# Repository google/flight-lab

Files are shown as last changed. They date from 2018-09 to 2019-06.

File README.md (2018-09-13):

# Flight Lab

Flight Lab is a project to build high fidelity flight simulation experience.

Disclaimer: This is not an officially supported Google product.

# Flight Lab Repository

This repository contains complete spec, design, model, source code of software
and firmware to build a flight simulation system.

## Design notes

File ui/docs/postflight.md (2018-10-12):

| ENGINE SHUTDOWN | |
|--|--|
| 1. Throttle | IDLE |
| 2. AVIONICS Switch | (BUS 1 and BUS 2) OFF |
| 3. Mixture | IDLE CUTOFF, Wait until engine stops. |
| 4. IGNITION Switch | OFF |
| 5. MASTER Switch | (ALT and BAT) OFF |

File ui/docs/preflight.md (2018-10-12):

| preflight | |
|--|--|
| 1. IGNITION Switch | OFF |
| 2. AVIONICS Switch | (BUS 1 and BUS 2) OFF |
| 3. MASTER Switch | (ALT and BAT) OFF |
| 4. All Light Switches | OFF |
| 5. PITOT HEAT Switch | OFF |
| 6. Throttle | IDLE |
| 7. Mixture | IDLE CUTOFF |
| 8. FLAPS | UP |

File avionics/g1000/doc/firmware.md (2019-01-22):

# Flashing the firmware

1. Load firmware/g1000.ino into Arduino IDE.
2. Set your sketchbook location to the avionics directory (Under preferences).
3. Install support for the [Feather M0 Proto](https://learn.adafruit.com/adafruit-feather-m0-basic-proto/using-with-arduino-ide).
4. Comment out either "#define PFD" or "#define MFD" at the top of the file.
   If this will be the PFD, leave MFD commented.  Otherwise comment out PFD
   and uncomment MFD.
5. Connect the Arduino to your PC with a micro USB cable.
6. Set the board to "Feather M0 Proto" under "Tools > Board"
7. Set the port under "Tools > Port".
8. Select "Sketch > Upload".
9. Done!

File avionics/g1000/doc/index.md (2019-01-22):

# Building the G1000

* [Bill of Materials](bom.md)
* [Ordering the PCBs](pcb_order.md)
* [Fabrication and Assembly](fabrication.md)
* [Building the PCBs](pcb_build.md)
* [Flashing the firmware](firmware.md)

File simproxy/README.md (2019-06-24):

# Prerequisites

* Microsoft Flight Simulator X with SP2
* Microsoft Flight Simulator X SP2 SDK

If Prepar3D is used instead, please update SIMCONNECT_SDK_DIR in Makefile to "C:\Program Files (x86)\Lockheed Martin\Prepar3D [version]\Utilities\SimConnect SDK".

# Setup

From command line, run the following in simproxy directory:

```
    make init
```

## gRPC

SimProxy depends on gRPC and related libraries.

Currently building these dependencies on Windows platform is not automated yet. Files have to be manually copied to [github root]\build\grpc.

```
    TODO: automate building of grpc on Windows platform.
```

# Build 

From command line, run the following in simproxy directory:

```
    make build
```

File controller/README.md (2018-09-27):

# Controller

Controller is the backend of the simulation system. It coordinates all machines
and devices to perform tasks, such as turning on/off the sytem, collecting
status, etc.

There are two parts: server and client. All communication between server and
client is via [gRPC](https://github.com/grpc/grpc).

## Server

Server runs on a single machine and connects to all clients to act as central
control. It:

*   dispatches command to all clients
*   collect component status from all clients
*   serve http APIs to frontend/UI

## Client

Client runs on every machine and acts as worker for server. Based on
configuration, it:

*   loads components to control apps, devices, etc
*   reports status of components to server.

# Usage

## Prerequisites

### For Windows Platform

1.  Install Python 2.7

    Choose X86 version regardless if OS is 64bit.

2.  Install Make for Windows

    2.1. Download and install from
    http://gnuwin32.sourceforge.net/packages/make.htm

    2.2. Add "C:\Program Files (X86)\GnuWin32\bin" to System PATH

3.  Install Microsoft Visual C++ Compiler for Python 2.7

    https://www.microsoft.com/en-us/download/details.aspx?id=44266

## Build

1. Install all the dependencies:

	```shell
	make init
	```

1. Build source code:

	```shell
	make build
	```

## Install

To have server or client run automatically on reboot:

```shell
make install-client
```

```shell
make install-server
```

# Development

To run server or client manually:

```shell
make run-client
```

```shell
make run-server
```

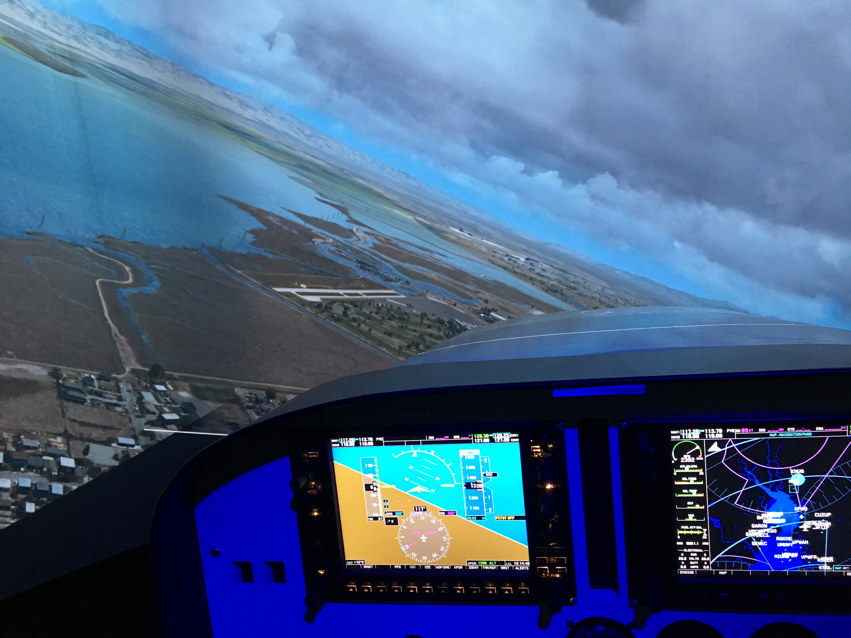
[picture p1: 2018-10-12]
ui/src/assets/bg.jpg

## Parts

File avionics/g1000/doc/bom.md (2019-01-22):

| Description | Quantity / G1000 | Manufacturer | Part Number | Link |
| --- | --- | --- | --- | --- |
| Arduino | 1 | Adafruit | Feather M0 Proto | [Adafruit](https://www.adafruit.com/products/2772)
| Button | 32 | C&K | KMT071 NGJ LHS | [Digikey](https://www.digikey.ca/product-detail/en/c-k/KMT071-NGJ-LHS/CKN10291CT-ND/2297282)
| Diode | 69 | Comchip Technology | CGRA4004-G | [Digikey](https://www.digikey.com/product-detail/en/comchip-technology/CGRA4004-G/641-1017-1-ND/1121139)
| 2 circuit OR gate | 1 | Fairchild Semi | NC7WZ32K8X | [Digikey](http://www.digikey.com/product-detail/en/fairchild-semiconductor/NC7WZ32K8X/NC7WZ32K8XCT-ND/965709)
| Rotary Encoder w/ Push | 3 | Bournes Inc | PEC11R-4215F-S0024 | [Digikey](https://www.digikey.com/product-detail/en/bourns-inc/PEC11R-4215F-S0024/PEC11R-4215F-S0024-ND/4499665)
| IDC Header | 4 | CNC Tech | 3020-20-0300-00 | [Digikey](https://www.digikey.com/product-detail/en/cnc-tech/3020-20-0300-00/1175-1623-ND/3441742)
| IDC Socket | 4 | CNC Tech | 3030-20-0103-00 | [Digikey](https://www.digikey.com/product-detail/en/cnc-tech/3030-20-0103-00/1175-1422-ND/3821475)
| Range Joystick | 1 | Grayhill | 60AD18-4-M-060C | [Digikey](https://www.digikey.com/products/en?mpart=60AD18-4-M-060C&v=136)
| Dual Rotary Encoder w/ Push | 5 | ELMA | E37-VT6330-1 | [Leobodnar](http://www.leobodnar.com/shop/index.php?main_page=product_info&cPath=98_75&products_id=196)
| Dual Knobs | 5 | ELMA | 020-4415 | [Leobodnar](http://www.leobodnar.com/shop/index.php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)
| LCD Controller | 1 | Chi Mei | M.NT68676.2A | [Ebay](http://www.ebay.com/itm/HDMI-VGA-DVI-lcd-Control-board-work-for-10-4inch-G104X1-L04-1024x768-lcd-panel-/181914630431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)
| LCD Panel | 1 | Chi Mei | G104XGE-L05 | [Ebay](https://www.ebay.com/sch/i.html?_from=R40&_trksid=m570.l1313&_nkw=G104XGE-L05&_sacat=0)
| LCD PSU | 1 | Chi Mei | | [Ebay](http://www.ebay.com/itm/New-12VDC-2-65A-40W-AC-Power-adapter-LCD-monitor-100VAC-240VAC-input-/181037711494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)

Note: The Grayhill 60A joystick can often be found on Ebay used for around $30.

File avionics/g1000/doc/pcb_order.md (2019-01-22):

# How To Order The Boards

## Chose a PCB Fabricator

Shop around with [PCBShopper](https://pcbshopper.com/) to find the best price
and quality.

## Upload the Gerber Files

Upload the following files one at a time to the PCB fabricator you've chosen:

* bottom/gerber_v3/bottom.zip
* left_side_autopilot/gerber_v3/left_side_auto.zip
* right_side/gerber_v3/right_side.zip

Note: Even if you don't want the GFC-700 autopilot, you should use the
left_side_autopilot files.  Just leave the autopilot buttons, diodes, and OR
gate unpopulated.  The files in left_side use a different kind of tactile
switch that proved very unreliable.

## Specify the PCB Parameters

* Layers: 2
* PCB thickness: 1.6mm
* Gold fingers: No
* Copper weight: 1oz

Note: This design contains internal cutouts.  Not all fabricators support
this.  We've had good results with both JLPCB and OSHPark.

You may want to order a solder stencil to save time.  We haven't done this,
but at times we wish we had.

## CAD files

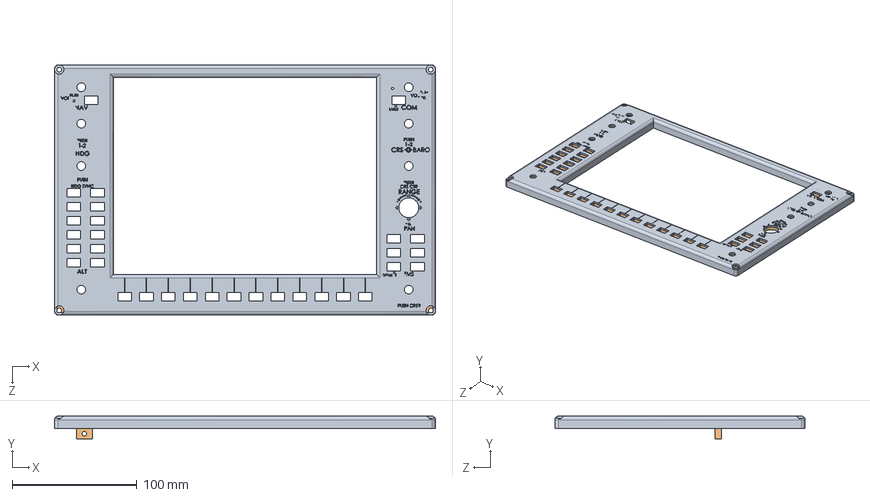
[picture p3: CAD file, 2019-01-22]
avionics/g1000/models/g1000_composite.SLDASM
306.0 x 18.4 x 201.0 mm
g1000
g1000_clear
g1000_text_new

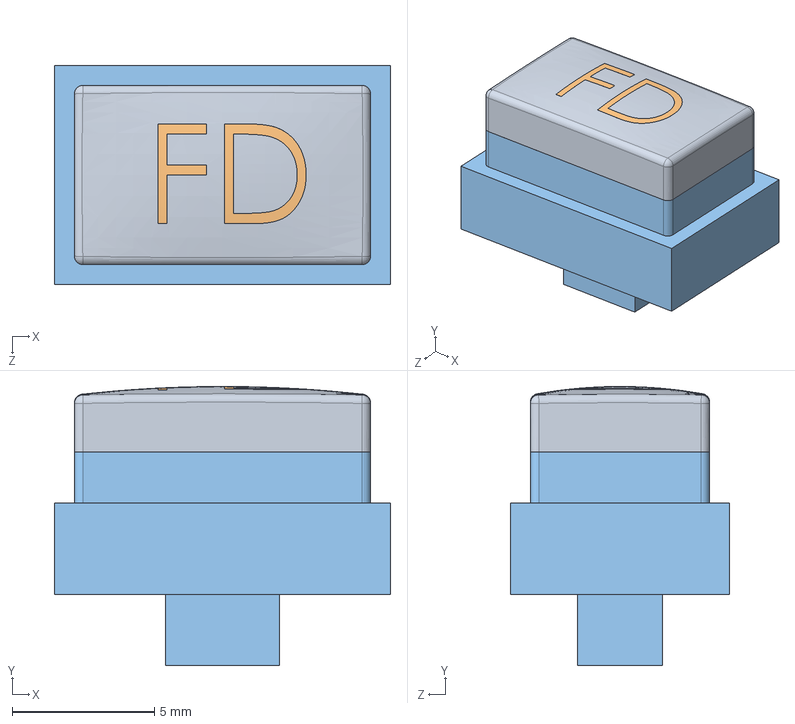
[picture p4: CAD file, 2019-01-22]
avionics/g1000/models/button_fd.SLDASM
11.8 x 9.80 x 7.70 mm
button_cap_fd
Part2^button_fd
button_base

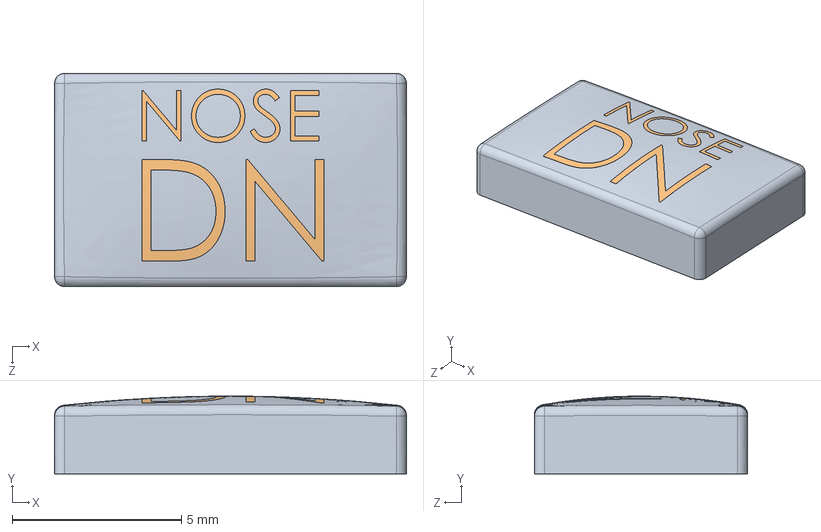
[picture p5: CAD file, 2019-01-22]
avionics/g1000/models/button_cap_down.SLDASM
10.4 x 2.30 x 6.30 mm
button_cap_down
Part11^button_cap_down

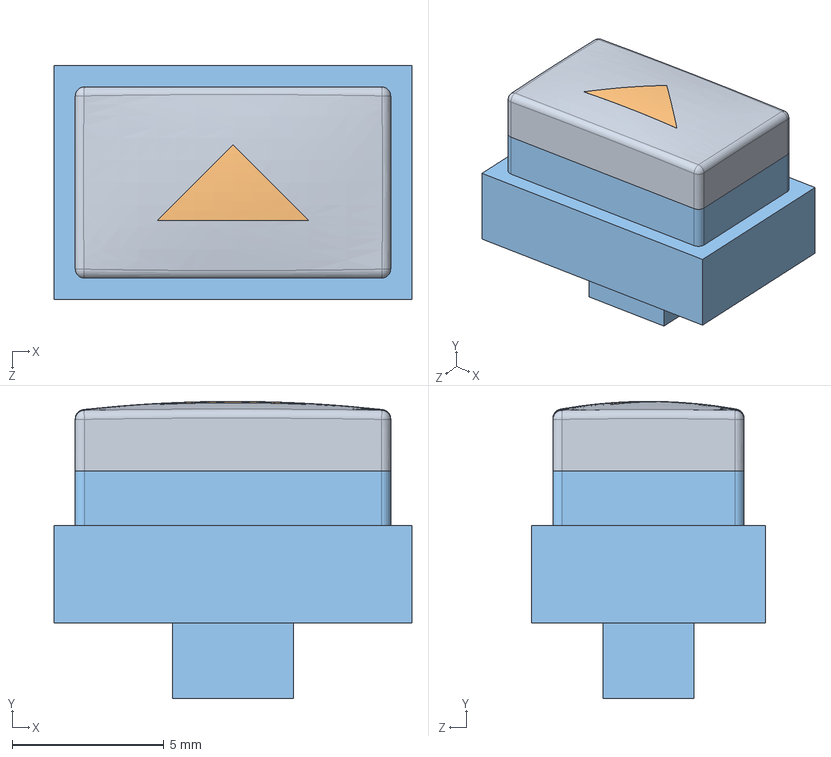
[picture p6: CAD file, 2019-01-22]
avionics/g1000/models/button_arrow.SLDASM
11.8 x 9.80 x 7.70 mm
button_cap_arrow
Part9^button_arrow
button_base

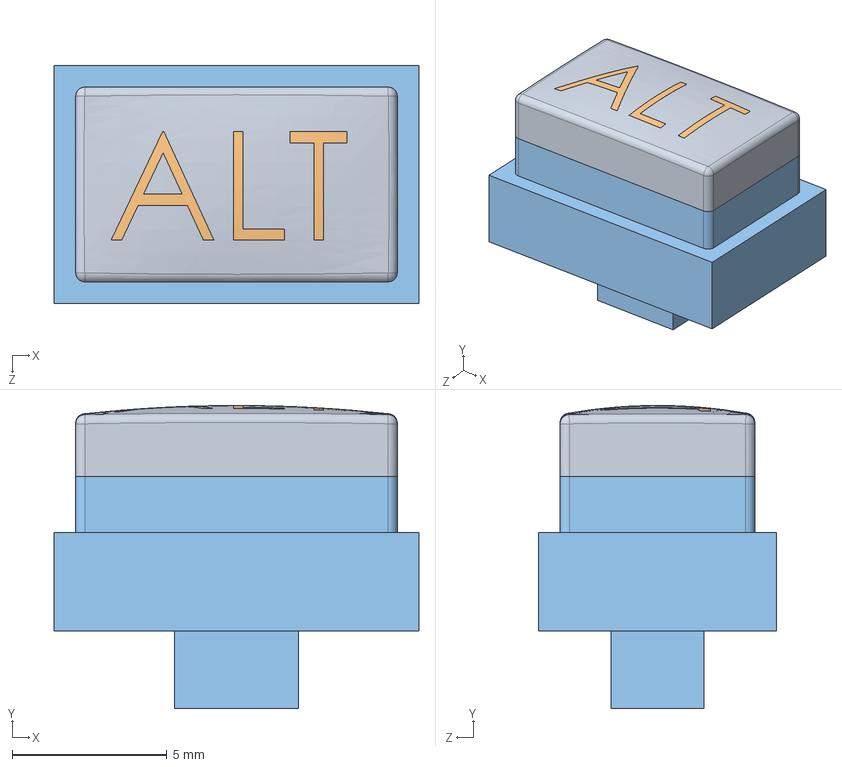
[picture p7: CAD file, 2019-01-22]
avionics/g1000/models/button_alt.SLDASM
11.8 x 9.80 x 7.70 mm
button_cap_alt
Part4^button_alt
button_base

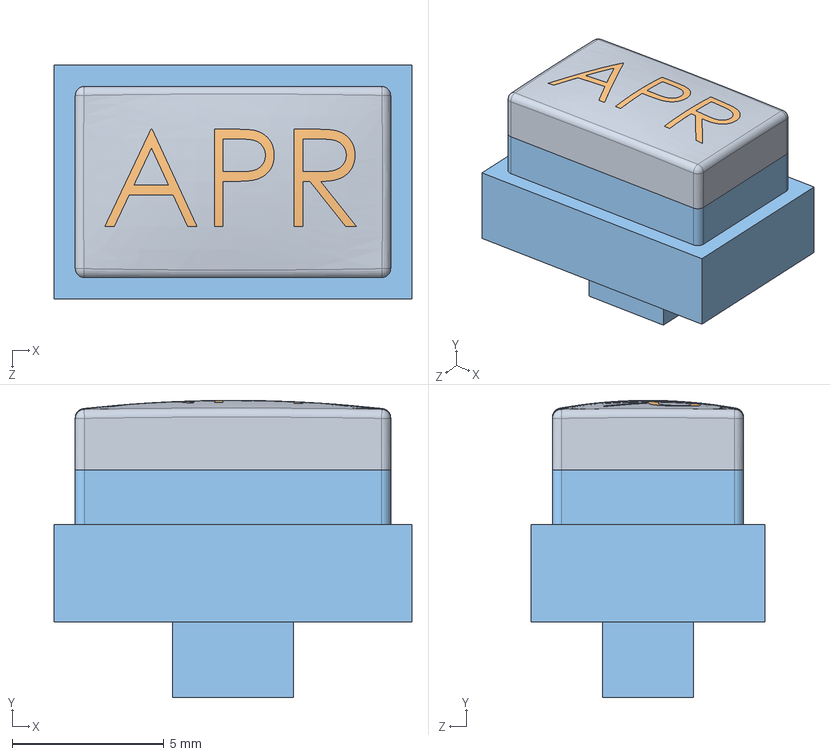
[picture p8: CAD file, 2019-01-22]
avionics/g1000/models/button_apr.SLDASM
11.8 x 9.80 x 7.70 mm
button_cap_apr
Part7^button_apr
button_base

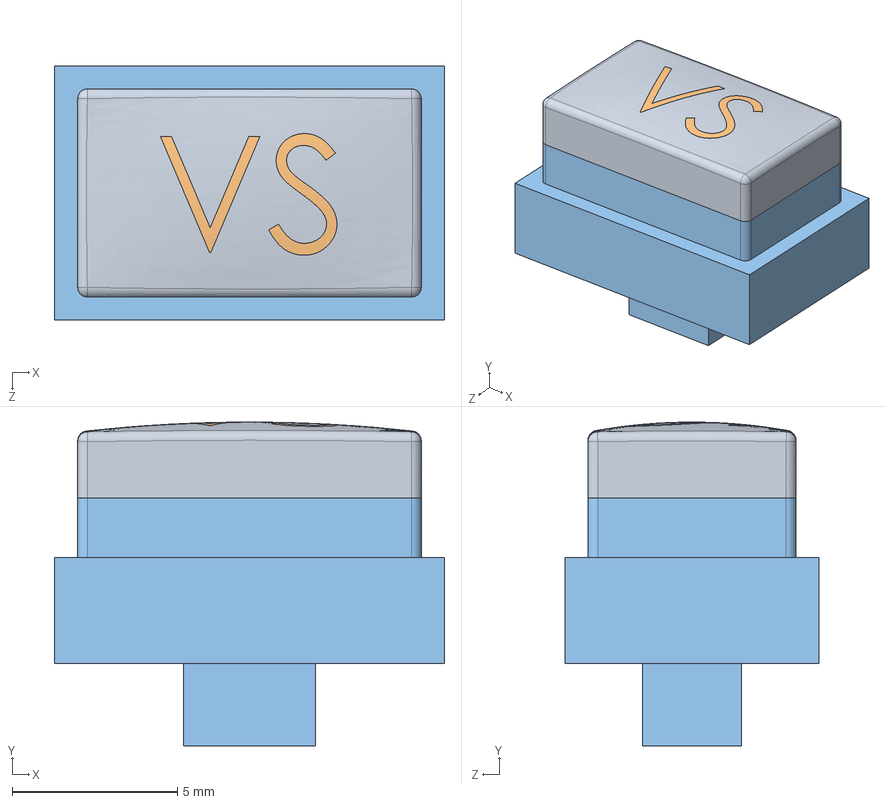
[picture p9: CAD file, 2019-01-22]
avionics/g1000/models/button_vs.SLDASM
11.8 x 9.80 x 7.70 mm
button_cap_vs
Part9^button_vs
button_base

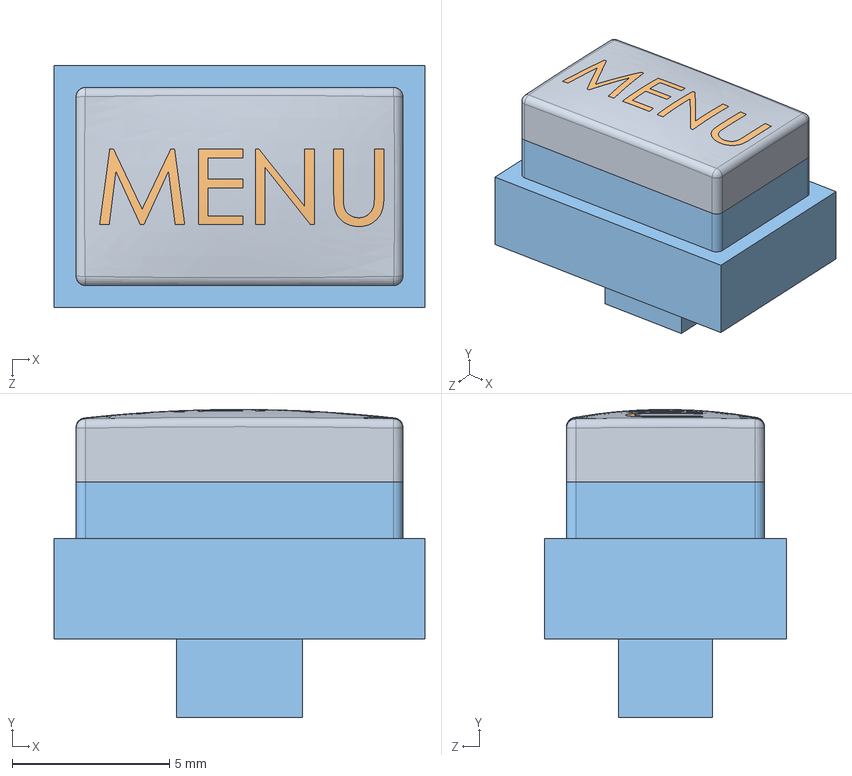
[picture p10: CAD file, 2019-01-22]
avionics/g1000/models/button_menu.SLDASM
11.8 x 9.80 x 7.70 mm
button_cap_menu
Part4^button_menu
button_base

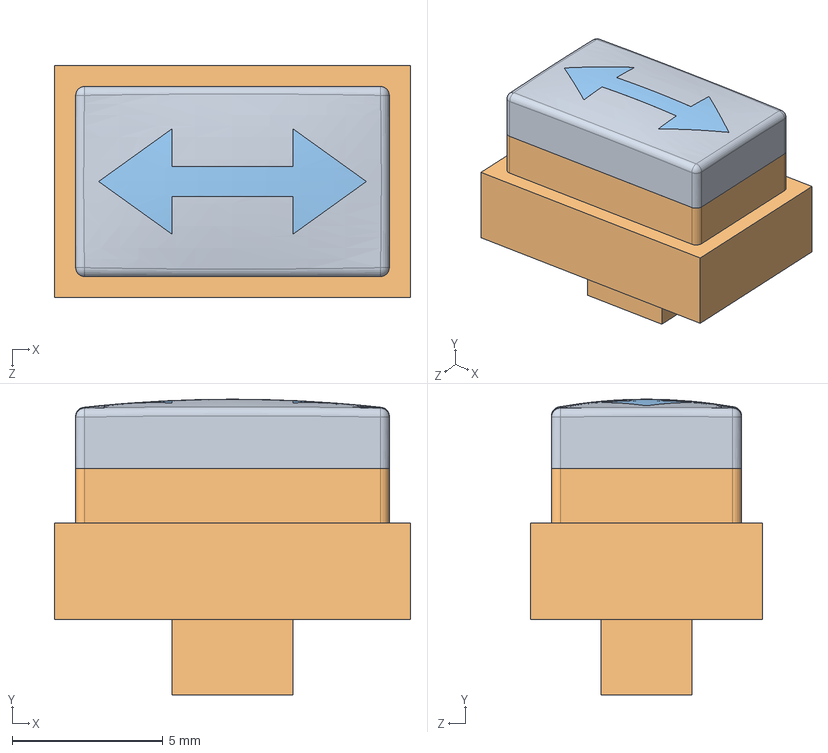
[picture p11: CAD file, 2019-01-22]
avionics/g1000/models/button_transfer.SLDASM
11.8 x 9.80 x 7.70 mm
button_cap_transfer
button_base
Part2^button_transfer

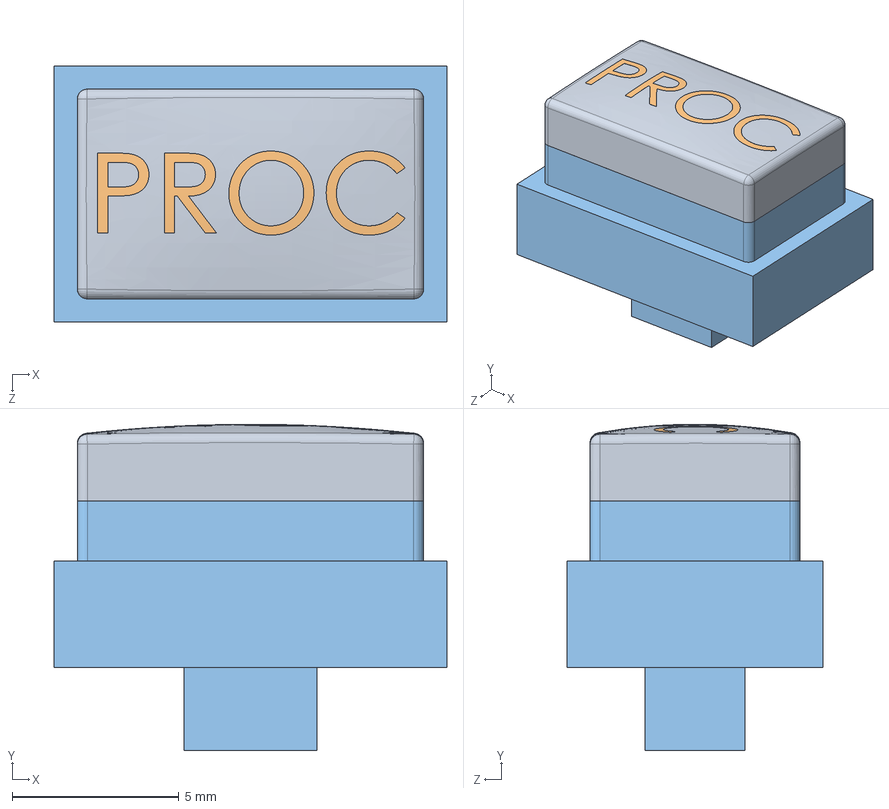
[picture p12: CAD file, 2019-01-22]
avionics/g1000/models/button_proc.SLDASM
11.8 x 9.80 x 7.70 mm
button_cap_proc
Part6^button_proc
button_base

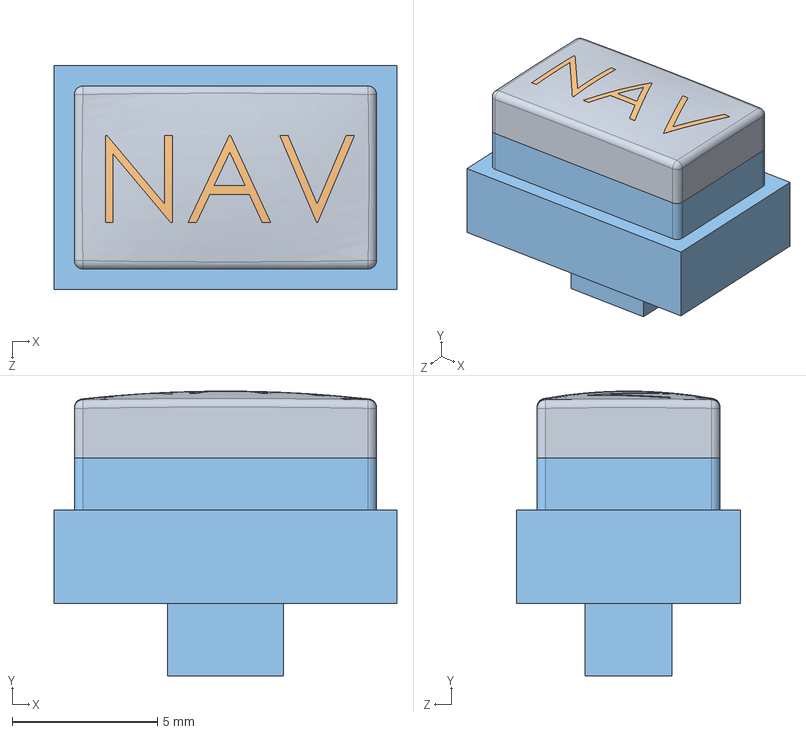
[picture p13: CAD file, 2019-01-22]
avionics/g1000/models/button_nav.SLDASM
11.8 x 9.80 x 7.70 mm
button_cap_nav
Part5^button_nav
button_base

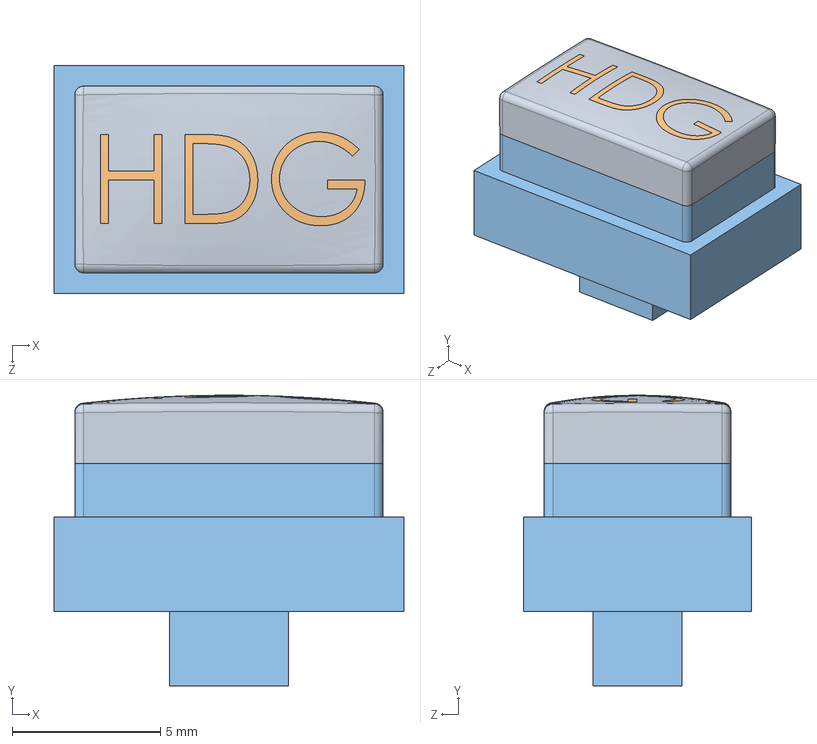
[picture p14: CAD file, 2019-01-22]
avionics/g1000/models/button_hdg.SLDASM
11.8 x 9.80 x 7.70 mm
button_cap_hdg
Part3^button_hdg
button_base

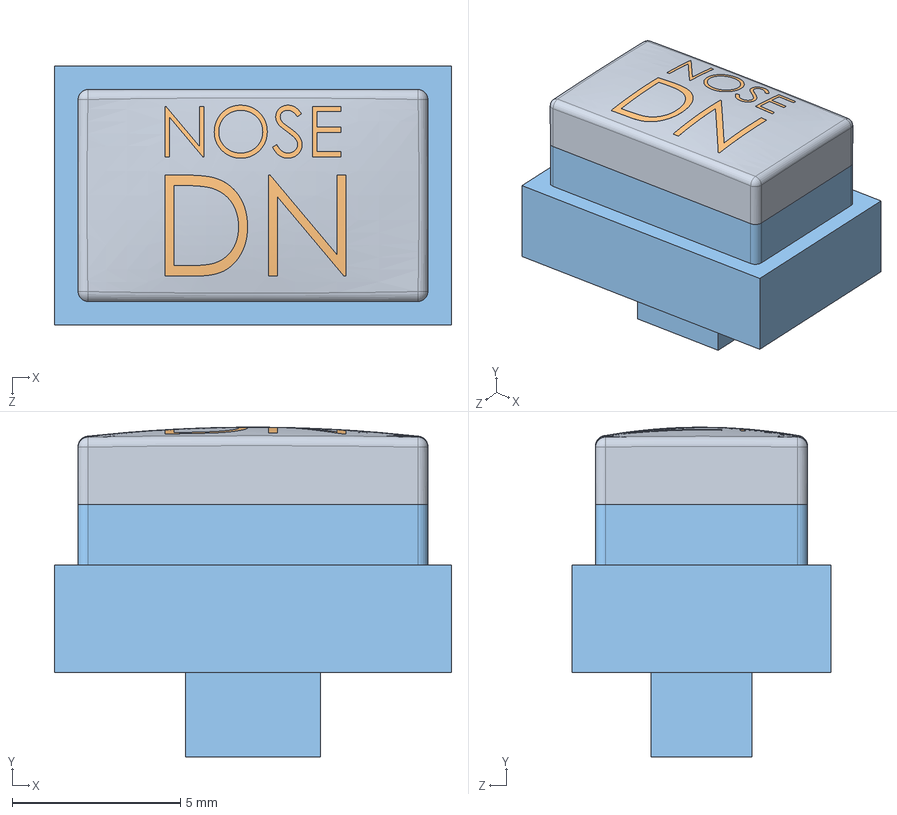
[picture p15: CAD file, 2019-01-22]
avionics/g1000/models/button_down.SLDASM
11.8 x 9.80 x 7.70 mm
button_cap_down
Part11^button_down
button_base

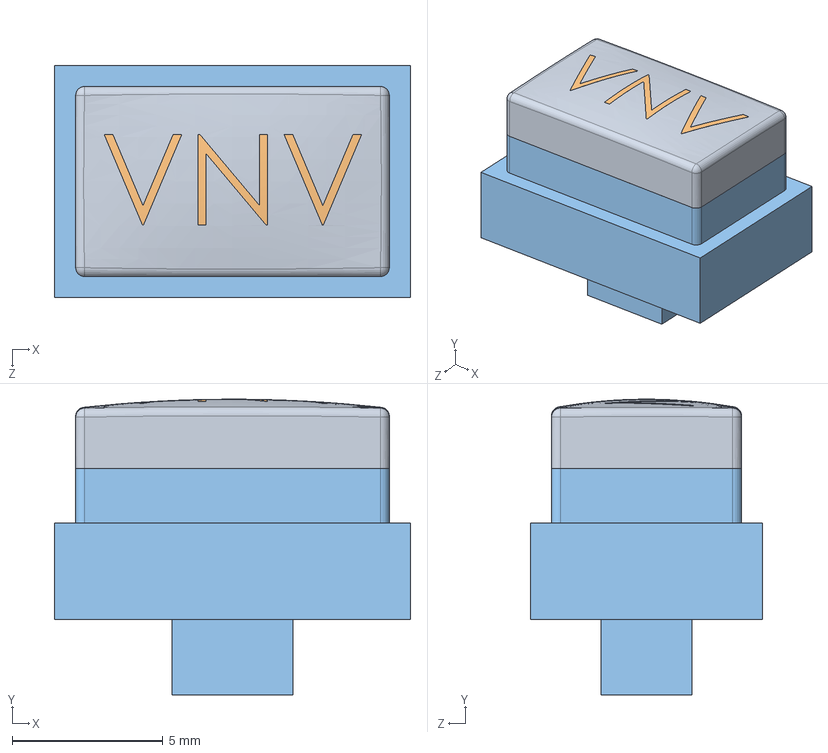
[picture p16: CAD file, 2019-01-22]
avionics/g1000/models/button_vnv.SLDASM
11.8 x 9.80 x 7.70 mm
button_cap_vnv
Part6^button_vnv
button_base

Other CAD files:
avionics/g1000/models/g1000_all.SLDASM
avionics/g1000/models/button_ap.SLDASM
avionics/g1000/models/button_clr.SLDASM
avionics/g1000/models/button_direct.SLDASM
avionics/g1000/models/button.SLDPRT
avionics/g1000/models/button_base.SLDPRT
avionics/g1000/models/button_bc.SLDASM
avionics/g1000/models/button_cap_alt.SLDPRT
avionics/g1000/models/button_cap_ap.SLDPRT
avionics/g1000/models/button_cap_apr.SLDPRT
avionics/g1000/models/button_cap_arrow.SLDPRT
avionics/g1000/models/button_cap_bc.SLDPRT
avionics/g1000/models/button_cap_clr.SLDPRT
avionics/g1000/models/button_cap_direct.SLDPRT
avionics/g1000/models/button_cap_down.SLDPRT
avionics/g1000/models/button_cap_ent.SLDPRT
avionics/g1000/models/button_cap_fd.SLDPRT
avionics/g1000/models/button_cap_flc.SLDPRT
avionics/g1000/models/button_cap_fpl.SLDPRT
avionics/g1000/models/button_cap_hdg.SLDPRT
avionics/g1000/models/button_cap_menu.SLDPRT
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

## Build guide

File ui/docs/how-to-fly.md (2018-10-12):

| engine start | |
|--|--|
| 1. Throttle | Open ¼ Inch |
| 2. MASTER Switch | (ALT and BAT) ON |
| 3. BEACON Light Switch | ON |
| 4. FUEL PUMP Switch | ON |
| 5. Mixture | FULL RICH |
| 6. FUEL PUMP Switch | OFF (after 3-5 seconds) |
| 7. IGNITION Switch | START Release when engine starts |
| 8. AVIONICS Switch | (BUS 1 and BUS 2) ON |

| before takeoff | |
|--|--|
| 1. Brake | APPLY |
| 2. Flight Controls | FREE and CORRECT |
| 3. Flight Instruments | CHECK (no red X’s) |
| 4. Altimeter | SET (PFD) |
| 5. ALT SEL | SET |
| 6. Standby Flight Instruments | CHECK |
| 7. Fuel Quantity | CHECK |
| 8. Mixture | RICH |
| 9. Elevator Trim | SET FOR TAKEOFF |
| 10. Throttle | 1800 RPM |
| 11. IGNITION Switch | CHECK L & R, drop < 150rpm, diff < 50rpm |
| 12. VAC Indicator | CHECK |
| 13. Engine Indicators | CHECK |
| 14. Ammeter & Voltmeter | CHECK |
| 15. Annunciators | CHECK |
| 16. Throttle | IDLE & CHECK |
| 17. Throttle | 1000 RPM |
| 18. COM Frequency | SET |
| 19. NAV Frequency | SET |
| 20. Flight Plan | As Desired |
| 21. Transponder | SET |
| 22. CDI Softkey | Select Nav Source |
| 22. FLAPS | UP to 10° |
| 23. STROBE Light Switch | ON |
| 24. Brake | RELEASE |

| NORMAL TAKEOFF | |
|--|--|
| 1. FLAPS | UP to 10° |
| 2. Throttle | FULL |
| 3. Mixture | RICH |
| 4. Elevator | Rotate at 55 KIAS |
| 5. Climb Airspeed | 70-80 KIAS |
| 6. FLAPS | RETRACT |

| ENROUTE CLIMB | |
|--|--|
| 1. Airspeed | 70 - 85 KIAS |
| 2. Throttle | FULL |
| 3. Mixture | RICH |

| CRUISE | |
|--|--|
| 1. Throttle | 2100 - 2700 RPM |
| 2. Elevator Trim | ADJUST |
| 3. Mixture | LEAN |

| DESCENT | |
|--|--|
| 1. Throttle | As Desired |
| 2. Mixture | ADJUST |
| 3. Altimeter | SET (PFD) |
| 4. ALT SEL | SET |
| 5. CDI Softkey | Select Nav Source |

| BEFORE LANDING | |
|--|--|
| 1. Mixture | RICH |
| 2. LAND & TAXI Light Switch | ON |

| NORMAL LANDING | |
|--|--|
| 1. Airspeed | 65 - 75 KIAS |
| 2. FLAPS | UP to 10° (<110 KIAS), 10° to FULL (<85 KIAS) |
| 3. Airspeed | 60 - 70 KIAS |
| 4. Elevator Trim | ADJUST |
| 5. Touchdown | Main Wheels First |
| 6. Landing Roll | Lower Nose Wheel Gently |
| 7. Brake | Minimum Required |

| AFTER LANDING | |
|--|--|
| 1. FLAPS | UP |
| 2. LAND Light Switch | OFF |
| 3. STROBE Light Switch | OFF |

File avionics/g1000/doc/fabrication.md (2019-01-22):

# Parts Fabrication

## Front Panel

There are a couple of options for fabricating the front panel.

### Using a multi-material 3d printer (preferrably SLA)

Pros:

* High quality result.
* Supports backlighting.
* Minimal post-processing.

Cons:

* Requires expensive equipment.

This approach requires a multi-material printer with very fine resolution.  The
printer will be creating small font text on the face plate, so precision is
essential.  These steps have been tested on an Objet500.

#### Print the parts

Print the following parts using the colors specified.  Look in models/v2_release
for the STL files.

* g1000_composite - g1000_clear-1.STL: 50/50 Clear and White

These two parts should be printed together.  Ensure that they share a common
origin.

* g1000_composite - g1000-1.STL: Black
* g1000_composite - g1000_ text_new-1.STL: White

The bulk of the frame is a 50/50 mix of clear and white.  This gives a good
compromise between light diffusion and transmission.

#### Finish the parts

* Use plastic scrapers and brushes under running water to remove the support
  material.
* Sand the front panel with 220 and then 400 grit sandpaper.
* Apply spray on clear coat.

#### Apply shielding

The one drawback of this approach is that the black frame is partially
translucent.  This means we need something to fully block the light in the
non-text areas.

We have had ok results using a layer of aluminum foil between the front panel
and the clear core.  The aluminum is cut to fit in the recess with an exacto
knife.  Then cutouts are added everywhere there is text or graphics.  This
blocks the light very well, but it is difficult to avoid tearing the foil.

In the future we may experiment with stencils and black spray paint or laser
cut paper shields.

### Using a desktop FDM 3D printer

Pros:

* Cheap
* May support backlighting

Cons:

* Labor intensive
* Experimental.

#### Print the parts

Print the following parts.  Look in models/v2_release for the STL files.

* left_side.STL
* right_side.STL

If you plan to use backlighting, these parts must be clear.  It is also
recommended that you use a high strength plastic with low warping such as
PETG.

#### Sanding and assembly

Sand until your hands ache.  It may also be worthwhile to use an expoxy filler
such as XTC-3D.  Then assemble the two halves using m3 square nuts and m3x25
hex socket cap screws.

#### Text options

* Print the text on a transparency sheet and glue the transparency to the frame.
  Then mask off the transparency and spray paint the rest of the frame black.
  Untested.
* Print the text on label paper and apply the labels to the frame.  Mask off the
  labels and spray paint the rest of the frame black.  Apply a layer of clear
  coat to seal the label to the frame.  This method is NOT compatible with
  backlighting.  Optional: Better results can be achieved by applying MANY
  layers of Mod Podge on top of the label before adding clear coat.  Eventually
  the label is encased in the Mod Podge and looks like it is part of the plastic
  frame.  Finish with clear coat.

## Buttons

### Using a multi-material 3d printer (preferrably SLA)

See the instructions for the face plate for more detail.  Each button should
be printed using the colors specified.  Look in models/v2_release
for the STL files.  Each button is made of three parts that must be printed
with a common origin.

* button_$NAME - button_base-1.STL: 50/50 clear and white
* button_$NAME - button_cap_$NAME-1.STL: Black
* button_$NAME - Part#^button_$NAME-1.STL: White

Here are the quantities needed:

* button_arrow: 12
* button_transfer: 2
* All other buttons: 1 each

### Using a desktop FDM 3D printer

In theory this could be done in the same manner as the frame.  However, doing
so would require an enormous amount of tedious labor.  This has not been
attempted.

## Monitor support

3D Print models/v2_release/screen_mount.STL.  Use whatever method is convenient.
If using an FDM printer, you'll need to generate supports in your slicer.

## Assembly

* Nest the clear frame core into the black face plate. Be sure to include
  the foil or paper light filter.
* If using backlighting, insert LED strip lighting into the channel around the
  edge with the LEDs facing inward.
* Insert all the buttons into their holes.
* Insert the three PCBs into their slots.  Attach with #6-32 screws.
* Attach the encoders to the frame with the nuts that came with them.
* Attach the monitor control boards to the monitor support with #6-32 and
  #4-40 screws.
* Lay the monitor on top of the back of the frame.  Lay the monitor support
  on top of it, aligning with the holes in the frame.
* Route the cables from the monitor control board to the monitor through the
  monitor support.
* Attach the monitor support to the frame with #6-32 screws.  Use caution around
  the ribbon cable on the right side.  It can bind against the monitor support
  and become damaged.
* The G1000 is complete!  Plug in the HDMI, power, and USB cables and test!
* Install into the instrument panel with #6-32 screws.

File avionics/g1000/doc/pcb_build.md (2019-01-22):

# Building the Boards

## Warning

If you haven't gotten the frame 3d printed yet, now is the time to do so.
You'll need it when you want to install the dual encoders.

## SMD Components

There are a large number of SMD components to install.  We highly recommend you
use solder paste and some combination of reflow and hot air instead of an iron.
It will save you a lot of time.

Pick a board, and start with the side that does not contain buttons. The buttons
are tiny and easily damaged by excess heat, so it's best to do them last.  We
use a pre-heater and hot air, so here's our process:

1. Lay down solder paste on all pads you intend to solder.  Don't worry if the
   paste isn't perfect or bridges.  It will fix itself when you apply heat.
2. Clamp the board on the pre-heater.
3. Lay the components down on the pads with fine tweezers.
4. Pre-heat the board to 180C.
5. Use a hot air gun at 250C to flow the solder.  Use the lowest air flow
   setting possible to avoid blowing the components around.
6. Turn off the pre-heater.

Repeat this process for the resistors and diodes on the other side.

**Pay careful attention to the polarity of the diodes.  A diode installed
backwards can be difficult to debug.  Make sure that the line on the diode is
installed on the same side as the line in the symbol on the PCB.**

## Teensy Tiny Buttons

Now you're ready to install the buttons.  These are essentially the same as
the other components, but greater care is warranted.  These buttons actually
specify that they should be installed according to this thermal profile:

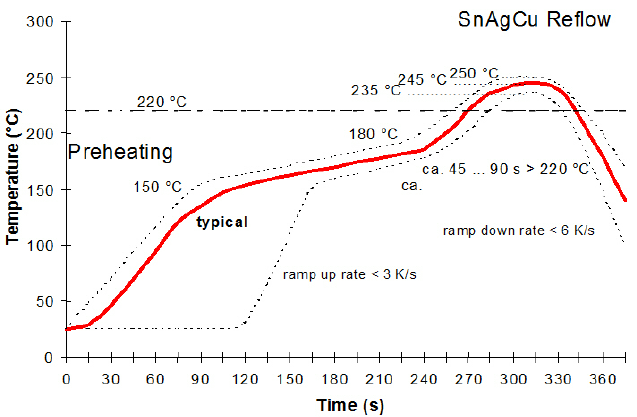
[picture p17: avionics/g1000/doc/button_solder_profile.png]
Button Thermal Profile


We used a timer and an infrared thermometer to match that profile as well as
our equipment was able.  Our experience was that the most critical part is to
keep the time spent above 200C as short as possible.  We were unable to ramp up
to 180C as fast as the chart specified, but that didn't seem to be a problem.
We didn't have to worry about ramp down speed since the board cooled slower than
6C/s even with all heat sources removed.

If you expose a button to excess heat, it will change color from pale yellow
to a brownish yellow.  This will cause the rubber dome to be brittle and it
will probably fail prematurely.  In this case, cover the other buttons with
Kapton tape and/or aluminum foil to shield them from more heat.  Then go
through the same heating steps as before to remove the bad component and
install a new one.  We found that the buttons could withstand several cycles
up to 180C without damage, but additional cycles to temperatures above 200C
caused problems.

## Pin Headers and Connectors

Install the pin headers and IDC connectors using a soldering iron.

## Caution

It's wise to do the encoder installs in stages because a mistake can cause
very odd errors that are hard to debug.  Start with a single encoder on the left
side.  Install the Arduino and make sure that encoder produces the expected
output on the serial port.  Then install another encoder and test.  After that,
connect the bottom board and test.  Finally connect the right board and install
those encoders one by one.

## Dual Encoders

The dual encoders stick through the holes in the PCB and are soldered to the
other side.  The thru-holes in the PCB are positioned so that they are offset
from the encoder pins by 2.54mm, which is the standard spacing for perfboard.

Buy some strip board and cut out 10 2x5 pieces.  The strips must run
along the short dimension so that you have 5 circuits with two holes each. The
easiest way to cut it is to clamp the boards in a vise with the lip of the
vise aligned with the cut you want to make.  Run a razor blade along the lip
of the vise 3 times on each side.  Then flex the board back and forth until it
breaks.

**Do not proceed further unless you have the 3d printed frame in hand!**

Place the dual encoders in the frame.  Refer to the pin labels on the back of
the encoders and the text on the PCB to make sure that the encoders are
installed right side up.  Once all the encoders are oriented correctly, place
the PCB in its slot in the frame.  Place a strip board on either side of an
encoder so that the encoder pins are connected to the pin headers on the PCB.
Securely fasten the encoder to the frame using the included nut.  Now you can
solder the pins to the perf board.  This procedure is necessary to make sure
the encoder sits at the correct height off of the PCB.

## Single Encoders

Solder the single encoders in place.  No special care is needed other than
making sure they sit flush on the PCB.

## Ribbon cables

TODO: Add notes here about the correct orientation.

## Joystick cable

TODO: Add notes about how to install the header on the joystick cable.

## Arduino Install

Solder the pin headers to the Arduino.  It's important to make sure they are
exactly vertical so it will fit in the socket on the board.  We recommend
putting the headers in a breadbord while soldering them to make sure they are
correct.

Install the Arduino on the left side PCB with the USB port facing down.

## Testing

Spin the encoders and push buttons while watching the serial console.  Make
sure you see all the events you expect and none that you don't.  If you
installed a diode backward, you may find that you will get spurious events
only when a certain encoder is in a certain position.  Thoroughly test each
encoder and its nearby components after you install each one.

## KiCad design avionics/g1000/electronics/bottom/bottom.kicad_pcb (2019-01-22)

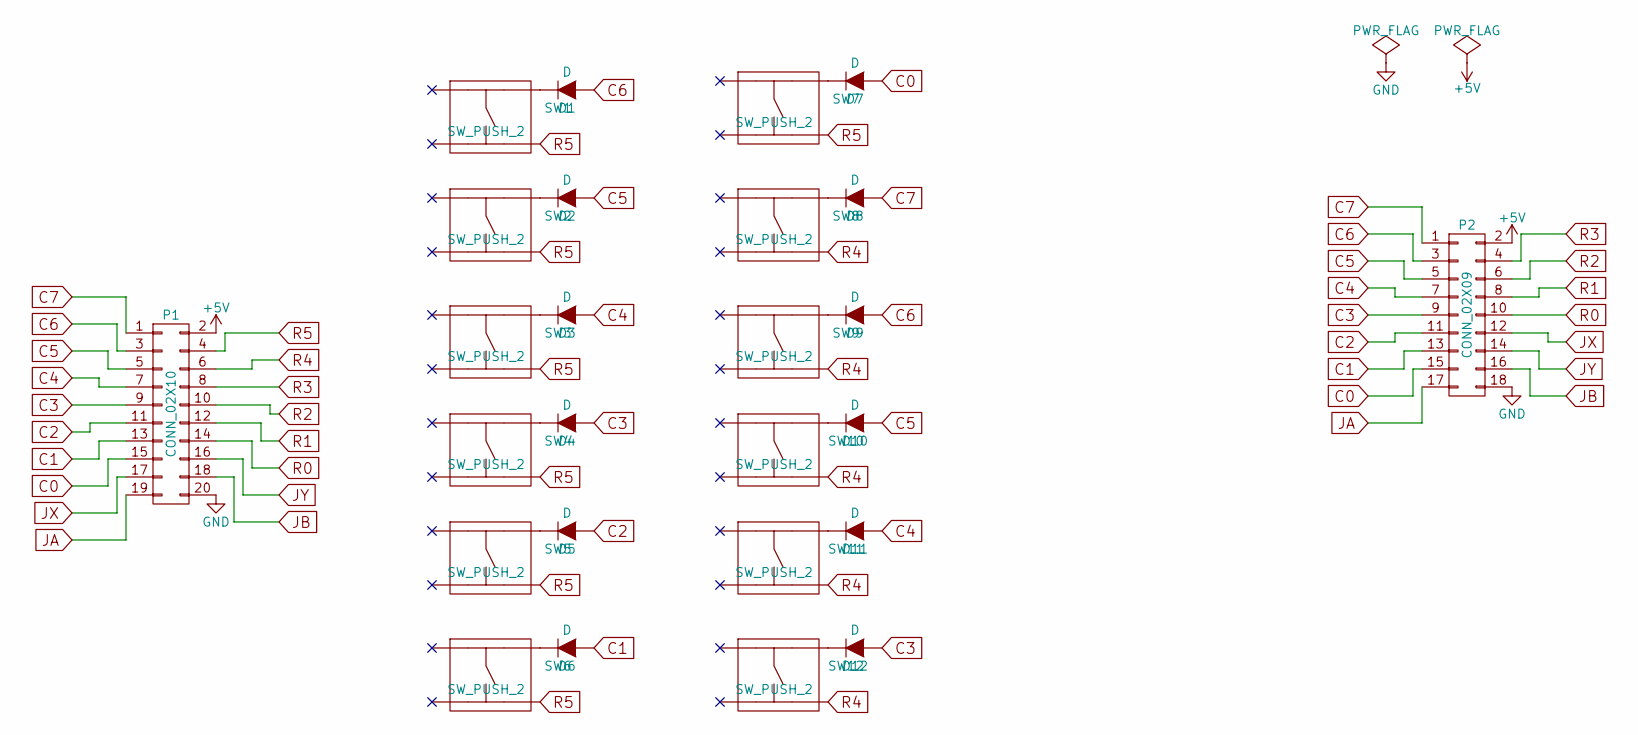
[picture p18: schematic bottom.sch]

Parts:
D1, D2, D3, D4, D5, D6, D7, D8, D9, D10, D11, D12: D; Diode_SMD
P1: CONN_02X10; CNC-3020-20
P2: CONN_02X09; CNC-3020-18
SW1, SW2, SW3, SW4, SW5, SW6, SW7, SW8, SW9, SW10, SW11, SW12: SW_PUSH_2; SW_PUSH

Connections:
+5V: P1.2, P2.2
C0: D7.2 (A), P1.15, P2.15
C1: D6.2 (A), P1.13, P2.13
C2: D5.2 (A), P1.11, P2.11
C3: D4.2 (A), D12.2 (A), P1.9, P2.9
C4: D3.2 (A), D11.2 (A), P1.7, P2.7
C5: D2.2 (A), D10.2 (A), P1.5, P2.5
C6: D1.2 (A), D9.2 (A), P1.3, P2.3
C7: D8.2 (A), P1.1, P2.1
GND: P1.20, P2.18
JA: P1.19, P2.17
JB: P1.18, P2.16
JX: P1.17, P2.12
JY: P1.16, P2.14
unnamed: D1.1 (K), SW1.2
unnamed: D2.1 (K), SW2.2
unnamed: D3.1 (K), SW3.2
unnamed: D4.1 (K), SW4.2
unnamed: D5.1 (K), SW5.2
unnamed: D6.1 (K), SW6.2
unnamed: D7.1 (K), SW7.2
unnamed: D8.1 (K), SW8.2
unnamed: D9.1 (K), SW9.2
unnamed: D10.1 (K), SW10.2
unnamed: D11.1 (K), SW11.2
unnamed: D12.1 (K), SW12.2
R0: P1.14, P2.10
R1: P1.12, P2.8
R2: P1.10, P2.6
R3: P1.8, P2.4
R4: P1.6, SW8.4, SW9.4, SW10.4, SW11.4, SW12.4
R5: P1.4, SW1.4, SW2.4, SW3.4, SW4.4, SW5.4, SW6.4, SW7.4

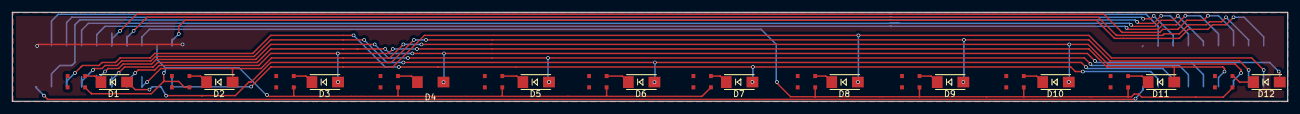
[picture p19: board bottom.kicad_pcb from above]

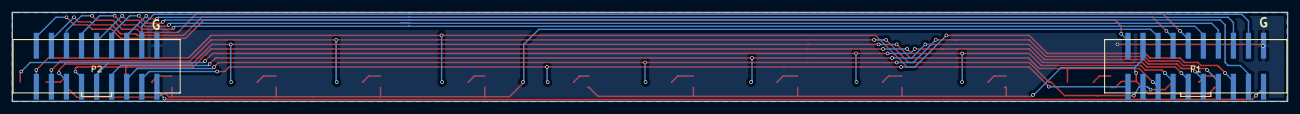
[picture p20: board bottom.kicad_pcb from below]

Board: 2 copper layers, 215.0 x 15.0 mm, 26 parts (2 on the bottom side), 32 nets.

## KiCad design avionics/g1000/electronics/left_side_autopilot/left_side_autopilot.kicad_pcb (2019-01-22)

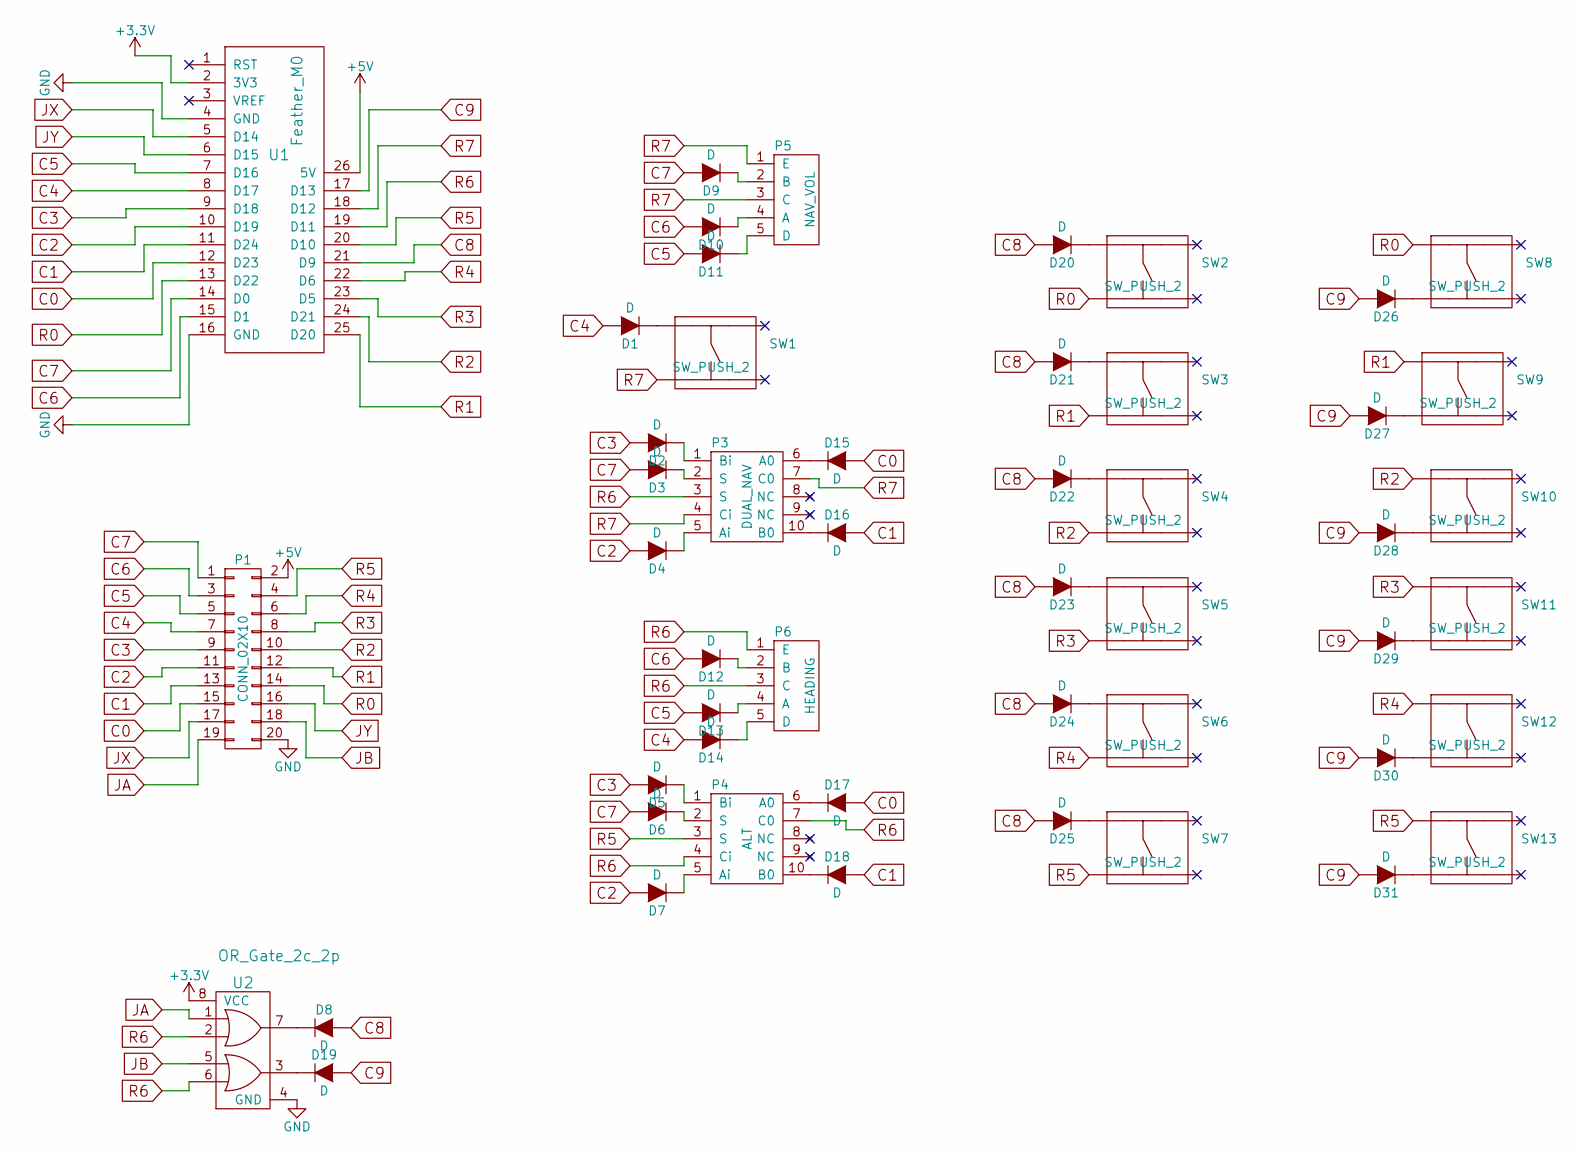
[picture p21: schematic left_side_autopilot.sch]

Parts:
D1, D2, D3, D4, D5, D6, D7, D8, D9, D10, D11, D12, D13, D14, D15, D16, D17, D18, D19, D20, D21, D22, D23, D24, D25, D26, D27, D28, D29, D30, D31: D; Diode_SMD
P1: CONN_02X10; CNC-3020-20
P3: DUAL_NAV; ELMA_conn
P4: ALT; ELMA_conn
P5: NAV_VOL; ENC_conn
P6: HEADING; ENC_conn
SW1, SW2, SW3, SW4, SW5, SW6, SW7, SW8, SW9, SW10, SW11, SW12, SW13: SW_PUSH_2; SW_PUSH
U1: Feather_M0; Feather_M0_SMD
U2: OR_Gate_2c_2p; NC7WZ32K8X

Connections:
+3V3: U1.2 (3V3), U2.8 (VCC)
+5V: P1.2, U1.26 (5V)
C0: D15.2 (A), D17.2 (A), P1.15, U1.12 (D23)
C1: D16.2 (A), D18.2 (A), P1.13, U1.11 (D24)
C2: D4.2 (A), D7.2 (A), P1.11, U1.10 (D19)
C3: D2.2 (A), D5.2 (A), P1.9, U1.9 (D18)
C4: D1.2 (A), D14.2 (A), P1.7, U1.8 (D17)
C5: D11.2 (A), D13.2 (A), P1.5, U1.7 (D16)
C6: D10.2 (A), D12.2 (A), P1.3, U1.15 (D1)
C7: D3.2 (A), D6.2 (A), D9.2 (A), P1.1, U1.14 (D0)
C8: D8.2 (A), D20.2 (A), D21.2 (A), D22.2 (A), D23.2 (A), D24.2 (A), D25.2 (A), U1.21 (D9)
C9: D19.2 (A), D26.2 (A), D27.2 (A), D28.2 (A), D29.2 (A), D30.2 (A), D31.2 (A), U1.17 (D13)
GND: P1.20, U1.4 (GND), U1.16 (GND), U2.4 (GND)
JA: P1.19, U2.1
JB: P1.18, U2.5
JX: P1.17, U1.5 (D14)
JY: P1.16, U1.6 (D15)
unnamed: D1.1 (K), SW1.1
unnamed: D2.1 (K), P3.1 (Bi)
unnamed: D3.1 (K), P3.2 (S)
unnamed: D4.1 (K), P3.5 (Ai)
unnamed: D5.1 (K), P4.1 (Bi)
unnamed: D6.1 (K), P4.2 (S)
unnamed: D7.1 (K), P4.5 (Ai)
unnamed: D8.1 (K), U2.7
unnamed: D9.1 (K), P5.2 (B)
unnamed: D10.1 (K), P5.4 (A)
unnamed: D11.1 (K), P5.5 (D)
unnamed: D12.1 (K), P6.2 (B)
unnamed: D13.1 (K), P6.4 (A)
unnamed: D14.1 (K), P6.5 (D)
unnamed: D15.1 (K), P3.6 (A0)
unnamed: D16.1 (K), P3.10 (B0)
unnamed: D17.1 (K), P4.6 (A0)
unnamed: D18.1 (K), P4.10 (B0)
unnamed: D19.1 (K), U2.3
unnamed: D20.1 (K), SW2.1
unnamed: D21.1 (K), SW3.1
unnamed: D22.1 (K), SW4.1
unnamed: D23.1 (K), SW5.1
unnamed: D24.1 (K), SW6.1
unnamed: D25.1 (K), SW7.1
unnamed: D26.1 (K), SW8.3
unnamed: D27.1 (K), SW9.3
unnamed: D28.1 (K), SW10.3
unnamed: D29.1 (K), SW11.3
unnamed: D30.1 (K), SW12.3
unnamed: D31.1 (K), SW13.3
R0: P1.14, SW2.3, SW8.1, U1.13 (D22)
R1: P1.12, SW3.3, SW9.1, U1.25 (D20)
R2: P1.10, SW4.3, SW10.1, U1.24 (D21)
R3: P1.8, SW5.3, SW11.1, U1.23 (D5)
R4: P1.6, SW6.3, SW12.1, U1.22 (D6)
R5: P1.4, P4.3 (S), SW7.3, SW13.1, U1.20 (D10)
R6: P3.3 (S), P4.4 (Ci), P4.7 (C0), P6.1 (E), P6.3 (C), U1.19 (D11), U2.2, U2.6
R7: P3.4 (Ci), P3.7 (C0), P5.1 (E), P5.3 (C), SW1.3, U1.18 (D12)

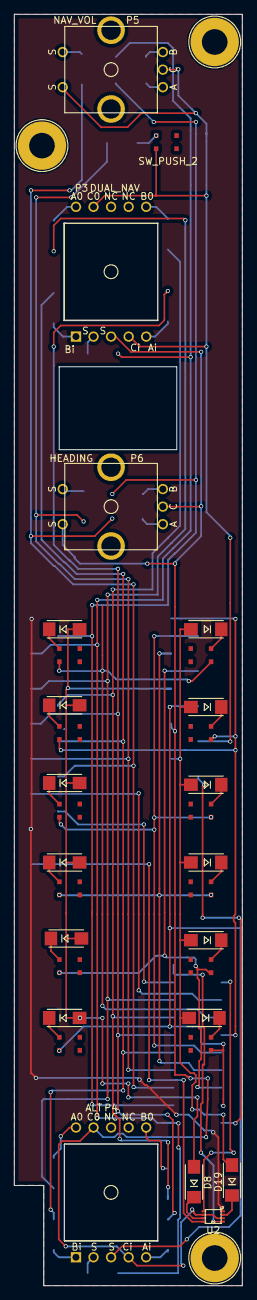
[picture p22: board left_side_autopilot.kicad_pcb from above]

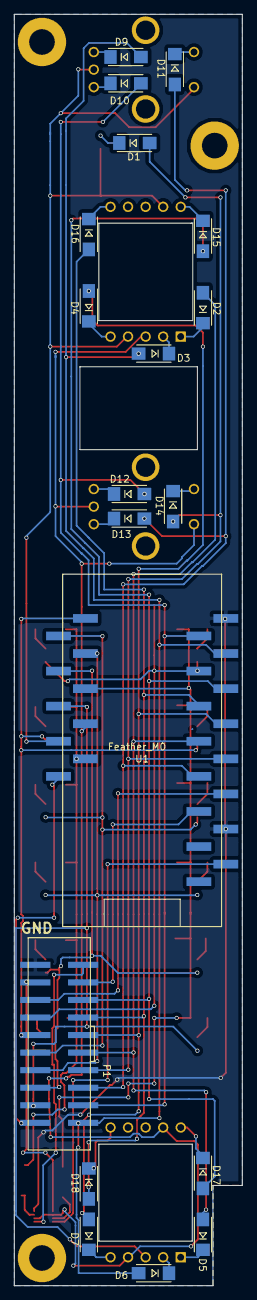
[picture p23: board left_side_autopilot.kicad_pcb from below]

Board: 2 copper layers, 33.0 x 184.0 mm, 54 parts (19 on the bottom side), 56 nets.

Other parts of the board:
Ref**: Val**; SCREW
Ref**#2, Ref**#3: Val**; SCREW

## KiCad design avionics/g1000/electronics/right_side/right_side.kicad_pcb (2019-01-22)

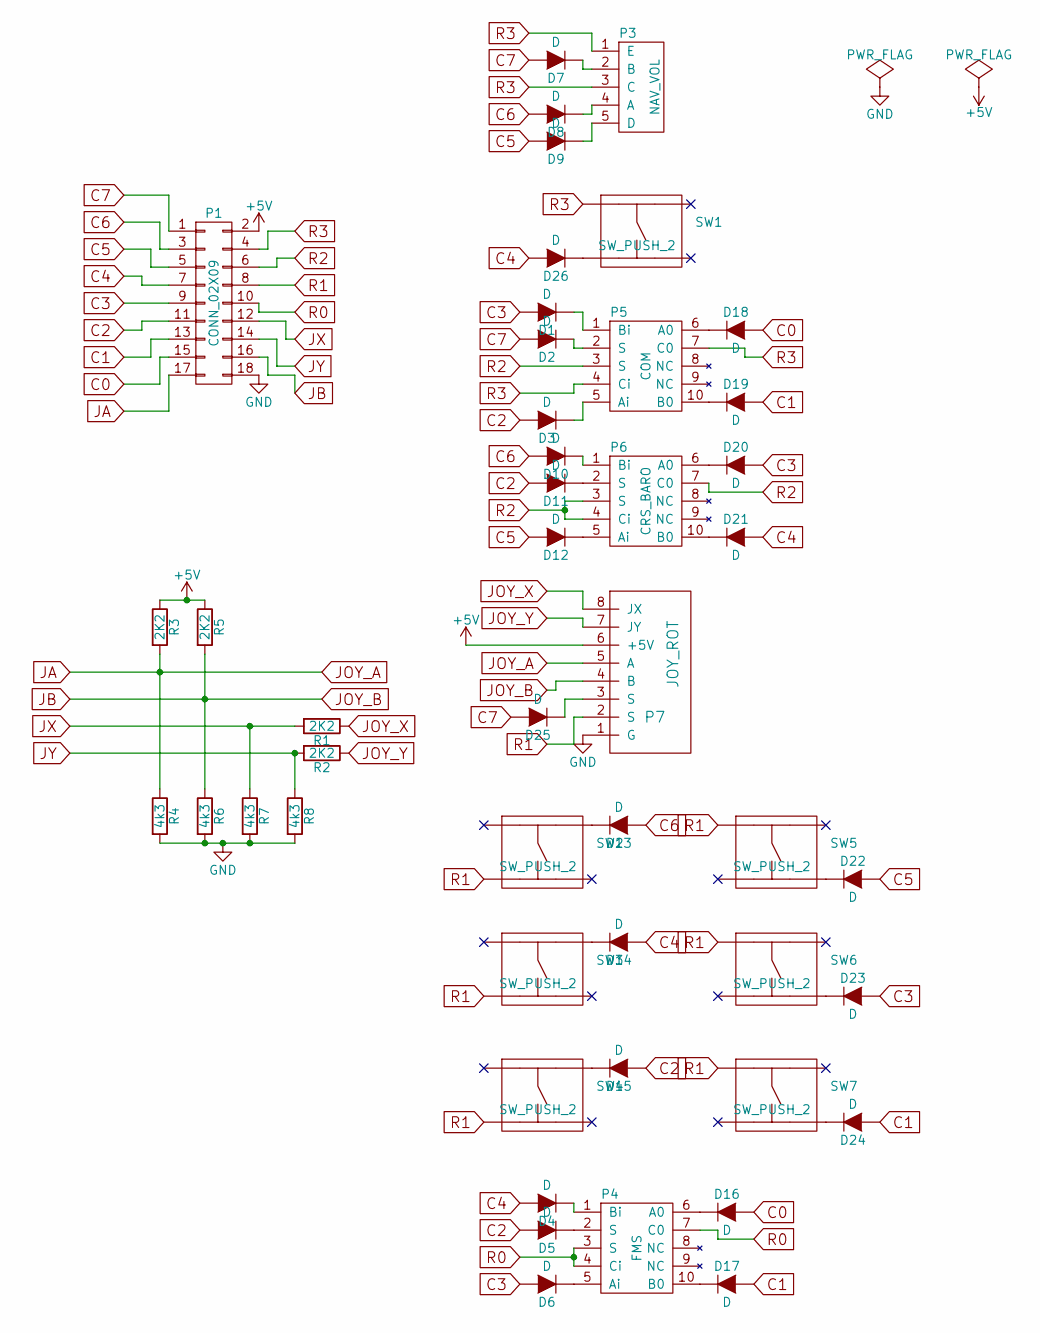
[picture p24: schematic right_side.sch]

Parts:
D1, D2, D3, D4, D5, D6, D7, D8, D9, D10, D11, D12, D13, D14, D15, D16, D17, D18, D19, D20, D21, D22, D23, D24, D25, D26: D; Diode_SMD
P1: CONN_02X09; CNC-3020-18
P3: NAV_VOL; ENC_conn
P4: FMS; ELMA_conn
P5: COM; ELMA_conn
P6: CRS_BARO; ELMA_conn
P7: JOY_ROT
R1, R2, R3, R5: 2K2; R_0805
R4, R6, R7, R8: 4k3; R_0805
SW1, SW2, SW3, SW4, SW5, SW6, SW7: SW_PUSH_2; SW_PUSH

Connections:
+5V: P1.2, P7.6 (+5V), R3.1, R5.1
C0: D16.2 (A), D18.2 (A), P1.15
C1: D17.2 (A), D19.2 (A), D24.2 (A), P1.13
C2: D3.2 (A), D5.2 (A), D11.2 (A), D15.2 (A), P1.11
C3: D1.2 (A), D6.2 (A), D20.2 (A), D23.2 (A), P1.9
C4: D4.2 (A), D14.2 (A), D21.2 (A), D26.2 (A), P1.7
C5: D9.2 (A), D12.2 (A), D22.2 (A), P1.5
C6: D8.2 (A), D10.2 (A), D13.2 (A), P1.3
C7: D2.2 (A), D7.2 (A), D25.2 (A), P1.1
GND: P1.18, P7.1 (G), R4.2, R6.2, R7.2, R8.2
JA: P1.17, P7.5 (A), R3.2, R4.1
JB: P1.16, P7.4 (B), R5.2, R6.1
JOY_X: P7.8 (JX), R1.1
JOY_Y: P7.7 (JY), R2.1
JX: P1.12, R1.2, R7.1
JY: P1.14, R2.2, R8.1
unnamed: D1.1 (K), P5.1 (Bi)
unnamed: D2.1 (K), P5.2 (S)
unnamed: D3.1 (K), P5.5 (Ai)
unnamed: D4.1 (K), P4.1 (Bi)
unnamed: D5.1 (K), P4.2 (S)
unnamed: D6.1 (K), P4.5 (Ai)
unnamed: D7.1 (K), P3.2 (B)
unnamed: D8.1 (K), P3.4 (A)
unnamed: D9.1 (K), P3.5 (D)
unnamed: D10.1 (K), P6.1 (Bi)
unnamed: D11.1 (K), P6.2 (S)
unnamed: D12.1 (K), P6.5 (Ai)
unnamed: D13.1 (K), SW2.2
unnamed: D14.1 (K), SW3.2
unnamed: D15.1 (K), SW4.2
unnamed: D16.1 (K), P4.6 (A0)
unnamed: D17.1 (K), P4.10 (B0)
unnamed: D18.1 (K), P5.6 (A0)
unnamed: D19.1 (K), P5.10 (B0)
unnamed: D20.1 (K), P6.6 (A0)
unnamed: D21.1 (K), P6.10 (B0)
unnamed: D22.1 (K), SW5.4
unnamed: D23.1 (K), SW6.4
unnamed: D24.1 (K), SW7.4
unnamed: D25.1 (K), P7.3 (S)
unnamed: D26.1 (K), SW1.3
R0: P1.10, P4.3 (S), P4.4 (Ci), P4.7 (C0)
R1: P1.8, P7.2 (S), SW2.3, SW3.3, SW4.3, SW5.1, SW6.1, SW7.1
R2: P1.6, P5.3 (S), P6.3 (S), P6.4 (Ci), P6.7 (C0)
R3: P1.4, P3.1 (E), P3.3 (C), P5.4 (Ci), P5.7 (C0), SW1.1

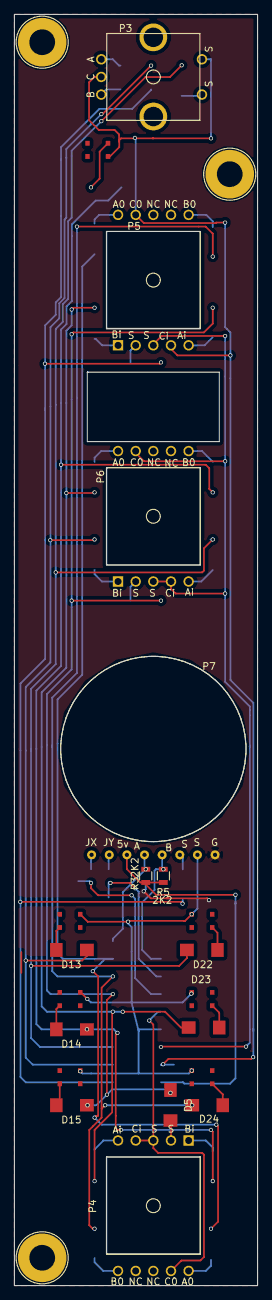
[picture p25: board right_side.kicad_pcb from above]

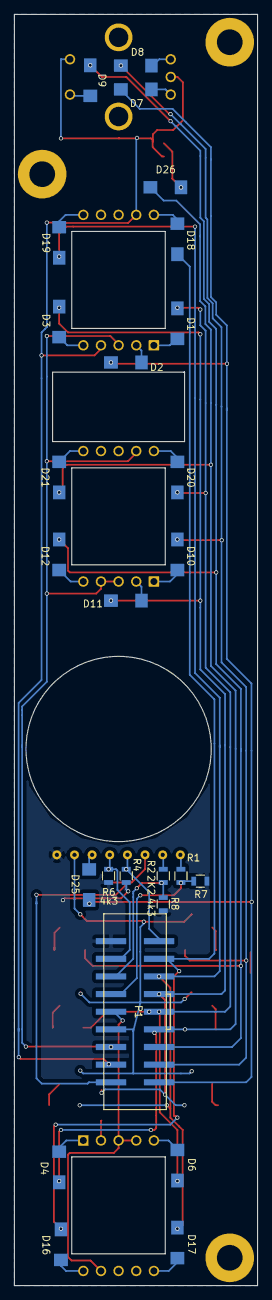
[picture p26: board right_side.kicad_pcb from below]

Board: 2 copper layers, 35.0 x 183.0 mm, 50 parts (26 on the bottom side), 46 nets.

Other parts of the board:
Ref**: Val**; SCREW
Ref**#2, Ref**#3: Val**; SCREW

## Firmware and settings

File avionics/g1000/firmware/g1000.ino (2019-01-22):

# Copyright 2018 Flight Lab authors.
#
# Licensed under the Apache License, Version 2.0 (the "License");
# you may not use this file except in compliance with the License.
# You may obtain a copy of the License at
#
#    https://www.apache.org/licenses/LICENSE-2.0
#
# Unless required by applicable law or agreed to in writing, software
# distributed under the License is distributed on an "AS IS" BASIS,
# WITHOUT WARRANTIES OR CONDITIONS OF ANY KIND, either express or implied.
# See the License for the specific language governing permissions and
# limitations under the License.

#include "../../shared/firmware/serial_rx/serial_rx.h"

#define PFD
// #define MFD

#define GFC700

#define MAX_OUT 16
#ifdef GFC700
#define MATRIX_COLS 10
#else
#define MATRIX_COLS 8
#endif
#define MATRIX_ROWS 8
#define MAX_COMMAND_LENGTH 32
#define KEY_ENTER 176

// Mapping from physical pins to matrix column and row indices.
#ifdef GFC700
//                                 0   1   2   3   4   5   6   7  8  9
const PROGMEM int kRowPins[] =    {22, 20, 21, 5,  6,  10, 11, 12};
const PROGMEM int kColumnPins[] = {23, 24, 19, 18, 17, 16, 1,  0, 9, 13};
#else
//                                 0   1   2   3   4   5   6   7
const PROGMEM int kRowPins[] =    {22, 20, 21, 5,  6,  10, 11, 12};
const PROGMEM int kColumnPins[] = {23, 24, 19, 18, 17, 16, 1,  0};
#endif

#ifdef PFD
#define IDENTIFIER "PFD"
#endif
#ifdef MFD
#define IDENTIFIER "MFD"
#endif

const PROGMEM char NAV_ID_TOGGLE[] = "NAV_ID_TOGGLE";
const PROGMEM char HDG_INCR[] = "HDG_INCR";
const PROGMEM char HDG_DECR[] = "HDG_DECR";
const PROGMEM char HDG_PRESS[] = "HDG_PRESS";
const PROGMEM char LARGE_ALT_INCR[] = "LARGE_ALT_INCR";
const PROGMEM char LARGE_ALT_DECR[] = "LARGE_ALT_DECR";
const PROGMEM char SMALL_ALT_INCR[] = "SMALL_ALT_INCR";
const PROGMEM char SMALL_ALT_DECR[] = "SMALL_ALT_DECR";
const PROGMEM char SMALL_ALT_PRESS[] = "SMALL_ALT_PRESS";
const PROGMEM char CRS_INCR[] = "CRS_INCR";
const PROGMEM char CRS_DECR[] = "CRS_DECR";
const PROGMEM char CRS_PRESS[] = "CRS_PRESS";
#ifdef PFD
const PROGMEM char NAV_FREQ_TOGGLE[] = "NAV_FREQ_TOGGLE";
const PROGMEM char LARGE_NAV_INCR[] = "LARGE_NAV_INCR";
const PROGMEM char LARGE_NAV_DECR[] = "LARGE_NAV_DECR";
const PROGMEM char SMALL_NAV_INCR[] = "SMALL_NAV_INCR";
const PROGMEM char SMALL_NAV_DECR[] = "SMALL_NAV_DECR";
const PROGMEM char SMALL_NAV_PRESS[] = "SMALL_NAV_PRESS";
const PROGMEM char COM_FREQ_TOGGLE[] = "COM_FREQ_TOGGLE";
const PROGMEM char COM_FREQ_TOGGLE_HOLD[] = "COM_FREQ_TOGGLE_HOLD";
const PROGMEM char LARGE_COM_INCR[] = "LARGE_COM_INCR";
const PROGMEM char LARGE_COM_DECR[] = "LARGE_COM_DECR";
const PROGMEM char SMALL_COM_INCR[] = "SMALL_COM_INCR";
const PROGMEM char SMALL_COM_DECR[] = "SMALL_COM_DECR";
const PROGMEM char SMALL_COM_PRESS[] = "SMALL_COM_PRESS";
const PROGMEM char BARO_INCR[] = "BARO_INCR";
const PROGMEM char BARO_DECR[] = "BARO_DECR";
const PROGMEM char RANGE_INCR[] = "PFD_RANGE_INCR";
const PROGMEM char RANGE_DECR[] = "PFD_RANGE_DECR";
const PROGMEM char RANGE_PRESS[] = "PFD_RANGE_PRESS";
const PROGMEM char RANGE_PAN_UP[] = "PFD_RANGE_PAN_UP";
const PROGMEM char RANGE_PAN_DOWN[] = "PFD_RANGE_PAN_DOWN";
const PROGMEM char RANGE_PAN_LEFT[] = "PFD_RANGE_PAN_LEFT";
const PROGMEM char RANGE_PAN_RIGHT[] = "PFD_RANGE_PAN_RIGHT";
const PROGMEM char DIRECT_TO[] = "PFD_DIRECT_TO";
const PROGMEM char MENU[] = "PFD_MENU";
const PROGMEM char FPL[] = "PFD_FPL";
const PROGMEM char PROC[] = "PFD_PROC";
const PROGMEM char CLR[] = "PFD_CLR";
const PROGMEM char ENT[] = "PFD_ENT";
const PROGMEM char LARGE_FMS_INCR[] = "PFD_LARGE_FMS_INCR";
const PROGMEM char LARGE_FMS_DECR[] = "PFD_LARGE_FMS_DECR";
const PROGMEM char SMALL_FMS_INCR[] = "PFD_SMALL_FMS_INCR";
const PROGMEM char SMALL_FMS_DECR[] = "PFD_SMALL_FMS_DECR";
const PROGMEM char SMALL_FMS_PRESS[] = "PFD_SMALL_FMS_PRESS";
const PROGMEM char SOFTKEY_1[] = "PFD_SOFTKEY_1";
const PROGMEM char SOFTKEY_2[] = "PFD_SOFTKEY_2";
const PROGMEM char SOFTKEY_3[] = "PFD_SOFTKEY_3";
const PROGMEM char SOFTKEY_4[] = "PFD_SOFTKEY_4";
const PROGMEM char SOFTKEY_5[] = "PFD_SOFTKEY_5";
const PROGMEM char SOFTKEY_6[] = "PFD_SOFTKEY_6";
const PROGMEM char SOFTKEY_7[] = "PFD_SOFTKEY_7";
const PROGMEM char SOFTKEY_8[] = "PFD_SOFTKEY_8";
const PROGMEM char SOFTKEY_9[] = "PFD_SOFTKEY_9";
const PROGMEM char SOFTKEY_10[] = "PFD_SOFTKEY_10";
const PROGMEM char SOFTKEY_11[] = "PFD_SOFTKEY_11";
const PROGMEM char SOFTKEY_12[] = "PFD_SOFTKEY_12";
#endif  // PFD
#ifdef MFD
const PROGMEM char NAV_FREQ_TOGGLE[] = "MFD_NAV_FREQ_TOGGLE";
const PROGMEM char LARGE_NAV_INCR[] = "MFD_LARGE_NAV_INCR";
const PROGMEM char LARGE_NAV_DECR[] = "MFD_LARGE_NAV_DECR";
const PROGMEM char SMALL_NAV_INCR[] = "MFD_SMALL_NAV_INCR";
const PROGMEM char SMALL_NAV_DECR[] = "MFD_SMALL_NAV_DECR";
const PROGMEM char SMALL_NAV_PRESS[] = "MFD_SMALL_NAV_PRESS";
const PROGMEM char COM_FREQ_TOGGLE[] = "MFD_COM_FREQ_TOGGLE";
const PROGMEM char COM_FREQ_TOGGLE_HOLD[] = "MFD_COM_FREQ_TOGGLE_HOLD";
const PROGMEM char LARGE_COM_INCR[] = "MFD_LARGE_COM_INCR";
const PROGMEM char LARGE_COM_DECR[] = "MFD_LARGE_COM_DECR";
const PROGMEM char SMALL_COM_INCR[] = "MFD_SMALL_COM_INCR";
const PROGMEM char SMALL_COM_DECR[] = "MFD_SMALL_COM_DECR";
const PROGMEM char SMALL_COM_PRESS[] = "MFD_SMALL_COM_PRESS";
const PROGMEM char BARO_INCR[] = "MFD_BARO_INCR";
const PROGMEM char BARO_DECR[] = "MFD_BARO_DECR";
const PROGMEM char RANGE_INCR[] = "MFD_RANGE_INCR";
const PROGMEM char RANGE_DECR[] = "MFD_RANGE_DECR";
const PROGMEM char RANGE_PRESS[] = "MFD_RANGE_PRESS";
const PROGMEM char RANGE_PAN_UP[] = "MFD_RANGE_PAN_UP";
const PROGMEM char RANGE_PAN_DOWN[] = "MFD_RANGE_PAN_DOWN";
const PROGMEM char RANGE_PAN_LEFT[] = "MFD_RANGE_PAN_LEFT";
const PROGMEM char RANGE_PAN_RIGHT[] = "MFD_RANGE_PAN_RIGHT";
const PROGMEM char DIRECT_TO[] = "MFD_DIRECT_TO";
const PROGMEM char MENU[] = "MFD_MENU";
const PROGMEM char FPL[] = "MFD_FPL";
const PROGMEM char PROC[] = "MFD_PROC";
const PROGMEM char CLR[] = "MFD_CLR";
const PROGMEM char ENT[] = "MFD_ENT";
const PROGMEM char LARGE_FMS_INCR[] = "MFD_LARGE_FMS_INCR";
const PROGMEM char LARGE_FMS_DECR[] = "MFD_LARGE_FMS_DECR";
const PROGMEM char SMALL_FMS_INCR[] = "MFD_SMALL_FMS_INCR";
const PROGMEM char SMALL_FMS_DECR[] = "MFD_SMALL_FMS_DECR";
const PROGMEM char SMALL_FMS_PRESS[] = "MFD_SMALL_FMS_PRESS";
const PROGMEM char SOFTKEY_1[] = "MFD_SOFTKEY_1";
const PROGMEM char SOFTKEY_2[] = "MFD_SOFTKEY_2";
const PROGMEM char SOFTKEY_3[] = "MFD_SOFTKEY_3";
const PROGMEM char SOFTKEY_4[] = "MFD_SOFTKEY_4";
const PROGMEM char SOFTKEY_5[] = "MFD_SOFTKEY_5";
const PROGMEM char SOFTKEY_6[] = "MFD_SOFTKEY_6";
const PROGMEM char SOFTKEY_7[] = "MFD_SOFTKEY_7";
const PROGMEM char SOFTKEY_8[] = "MFD_SOFTKEY_8";
const PROGMEM char SOFTKEY_9[] = "MFD_SOFTKEY_9";
const PROGMEM char SOFTKEY_10[] = "MFD_SOFTKEY_10";
const PROGMEM char SOFTKEY_11[] = "MFD_SOFTKEY_11";
const PROGMEM char SOFTKEY_12[] = "MFD_SOFTKEY_12";
#endif  // MFD

#ifdef GFC700
const char AFCS_AP[] = "AFCS_AP";
const char AFCS_HDG[] = "AFCS_HDG";
const char AFCS_NAV[] = "AFCS_NAV";
const char AFCS_APR[] = "AFCS_APR";
const char AFCS_VS[] = "AFCS_VS";
const char AFCS_FLC[] = "AFCS_FLC";
const char AFCS_FD[] = "AFCS_FD";
const char AFCS_ALT[] = "AFCS_ALT";
const char AFCS_VNV[] = "AFCS_VNV";
const char AFCS_BC[] = "AFCS_BC";
const char AFCS_UP[] = "AFCS_UP";
const char AFCS_DN[] = "AFCS_DN";
#endif  // GFC700

/*
 * TODO: Add support for these features:
 *
 * MFD_RANGE_PAN_HOLD
 * MFD_RANGE_PAN_RELEASE
 * COM_FREQ_TOGGLE_HOLD
 * MFD_CLR_HOLD
 * PFD Reversionary mode
 */

typedef const char *Control;

// Pure virtual base class for input handlers.
class InputHandler {
 public:
  // row_index and pin_a_index are required and must be valid indices into
  // kRowPins and kColumnPins.  pin_b_index is optional.
  InputHandler(int row_index, int pin_a_index, int pin_b_index = -1) :
      row_index_(row_index),
      pin_a_index_(pin_a_index),
      pin_b_index_(pin_b_index),
      row_pin_(kRowPins[row_index]),
      pin_a_(kColumnPins[pin_a_index]),
      pin_b_(pin_b_index > 0 ? kColumnPins[pin_b_index]: -1) {

  }

  // Return NULL if no event should be generated.  Otherwise return
  // event string.  All strings returned must be global constants.
  virtual Control trigger(int pin, int val) = 0;

  // Get the row and columns for associated pins.  Return -1 if the pin
  // is not populated.  A given input handler may not span multiple rows.
  int get_row() { return row_index_; }
  int get_pin_a_column() { return pin_a_index_; }
  int get_pin_b_column() { return pin_b_index_; }

 protected:
  int row_index_;
  int pin_a_index_;
  int pin_b_index_;
  int row_pin_;
  int pin_a_;
  int pin_b_;
};

// Input matrix handler.  Scans the matrix row by row looking for changes in
// pin states.  Triggers associated handlers when pin states change.
class InputMatrix {
 public:
  InputMatrix() : current_row_(0) {
    // Row pins are pulled low when being scanned.  Set them all high to
    // disable all rows on startup.
    for (int i = 0; i < MATRIX_ROWS; ++i) {
      pinMode(kRowPins[i], OUTPUT);
      digitalWrite(kRowPins[i], HIGH);
    }
    for (int i = 0; i < MATRIX_COLS; ++i) {
      pinMode(kColumnPins[i], INPUT_PULLUP);
    }

    // Scan the rows once with handlers suppressed to initialize last_vals_.
    for (int i = 0; i < MATRIX_ROWS; ++i) {
      scan_row(true);
    }
  }

  // Inserts an input handler into the matrix.  Caller retains ownership of
  // target. Returns false if target has invalid row or pin indices or if
  // target is null.
  bool insert(InputHandler *target) {
    if (NULL == target) return false;

    int row = target->get_row();
    int pin_a_column = target->get_pin_b_column();
    int pin_b_column = target->get_pin_b_column();

    if (row >= MATRIX_ROWS ||
        pin_a_column >= MATRIX_COLS ||
        pin_b_column >= MATRIX_COLS) {
      return false;
    }

    handlers_[row][pin_a_column] = target;

    if (pin_b_column >= 0) {
      handlers_[row][pin_b_column] = target;
    }
    return true;
  }

  // Scan the current row for pin state changes.
  void scan_row(bool suppress_handlers = false) {
    for (int i = 0; i < MATRIX_COLS; ++i) {
      InputHandler *handler = handlers_[current_row_][i];
      int val = digitalRead(kColumnPins[i]);
      int last = last_vals_[current_row_][i];
      last_vals_[current_row_][i] = val;

      if (suppress_handlers) continue;
      if (val == last) continue;
      if (NULL == handler) continue;

      Control result = handler->trigger(kColumnPins[i], val);
      if (NULL != result) {
        Serial.println(result);
      }
    }

    // Disable the current row, wait for voltages to settle, and move to the
    // next row.
    digitalWrite(kRowPins[current_row_], HIGH);
    delayMicroseconds(50);
    current_row_ = (current_row_ + 1) % MATRIX_ROWS;
    digitalWrite(kRowPins[current_row_], LOW);
  }

 private:
  // The index of the current row to be scanned.
  int current_row_;

  // Mapping from pin indices to input handlers.  The input handlers are
  // notified when their associated pins change state.
  InputHandler *handlers_[MATRIX_ROWS][MATRIX_COLS] = {};

  // Values seen at each matrix position on the last scan.
  int last_vals_[MATRIX_ROWS][MATRIX_COLS];
};

// Handles a simple active low momentary button.  No builtin debounce.
class Button : public InputHandler {
  Control control_;

 public:
  Button(Control control, int row_index, int col_index) :
      InputHandler(row_index, col_index),
      control_(control) {}

  virtual Control trigger(int pin, int val) {
    if (pin != pin_a_) return NULL;
    if (val == LOW && digitalRead(pin_a_) == LOW) return control_;
    return NULL;
  }
};

// Handles most quadrature encoders.
// Tested with ELMA E37 and Bournes PEC11R series.
// Set double_pulse = true for encoders that generate two pulses per detent.
class Encoder : public InputHandler {
 protected:
  Control left_control_;
  Control right_control_;
  bool double_pulse_;

 public:
  Encoder(Control left, Control right, int row_index, int pin_a_index,
          int pin_b_index, bool double_pulse = false)
      : InputHandler(row_index, pin_a_index, pin_b_index),
        left_control_(left),
        right_control_(right),
        double_pulse_(double_pulse) {}

  virtual Control trigger(int pin, int val) {
    if (pin == pin_a_ && LOW == val) {
      if (LOW == digitalRead(pin_b_)) {
        return left_control_;
      }
      return right_control_;
    }
    if (!double_pulse_ && pin == pin_b_ && HIGH == val) {
      if (LOW == digitalRead(pin_a_)) {
        return left_control_;
      }
      return right_control_;
    }
    return NULL;
  }
};

// Handles the quadrature encoder in a Grayhill 60A joystick / encoder.
// That encoder has a detent at every pin state change, which requires
// slightly different logic than the other encoders.
class OptoEncoder : public InputHandler {
  Control pin_a_changed_outputs_[2][2];
  Control pin_b_changed_outputs_[2][2];
  Control left_control_;
  Control right_control_;

 public:
  OptoEncoder(Control left, Control right, int row_index, int pin_a_index,
              int pin_b_index)
      : InputHandler(row_index, pin_a_index, pin_b_index),
        left_control_(left),
        right_control_(right),
        pin_a_changed_outputs_{{left, right}, {right, left}},
        pin_b_changed_outputs_{{right, left}, {left, right}} {}

  virtual Control trigger(int pin, int val) {
    if (pin == pin_a_) {
      int b_val = digitalRead(pin_b_);
      return pin_a_changed_outputs_[val == HIGH][b_val == HIGH];
    }
    if (pin == pin_b_) {
      int a_val = digitalRead(pin_a_);
      return pin_b_changed_outputs_[val == HIGH][a_val == HIGH];
    }
  }
};

// Handles the analog 2 axis joystick in a Grayhill 60A joystick / knob.
class Joystick {
#define ANALOG_MAX 1023
#define AXIS_COUNT 2

 public:
  Joystick(Control left, Control right, Control up, Control down, int pin_x,
           int pin_y) :
      skipped_scan_count_(0) {
    pins_[AXIS_X] = pin_x;
    pins_[AXIS_Y] = pin_y;

    // Initialize last_vals to a value that corresponds to a centered position.
    last_val_[AXIS_X] = 2;
    last_val_[AXIS_Y] = 2;

    low_control_[AXIS_X] = left;
    high_control_[AXIS_X] = right;
    low_control_[AXIS_Y] = down;
    high_control_[AXIS_Y] = up;
  }

  // Maybe scan the joystick for changes.
  void scan(void) {
    // analogRead is slow. We can only afford to do this once every 16
    // matrix scans.
    if (skipped_scan_count_ == 0) {
      scan_axis(AXIS_X);
      scan_axis(AXIS_Y);
    }
    skipped_scan_count_ = (skipped_scan_count_ + 1) % 16;
  }

 private:
  int pins_[AXIS_COUNT];
  int last_val_[AXIS_COUNT];
  int skipped_scan_count_;
  Control low_control_[AXIS_COUNT];
  Control high_control_[AXIS_COUNT];

  enum JoystickAxis {
    AXIS_X = 0,
    AXIS_Y,
  };

  Control trigger_axis(JoystickAxis axis, int val) {
    switch (val) {
      case 0:
        return low_control_[axis];
      case 5:
        return high_control_[axis];
      default:
        return NULL;
    }
  }

  void scan_axis(JoystickAxis axis) {
    int val = analogRead(pins_[axis]);
    if (val > ANALOG_MAX) val = ANALOG_MAX;
    val = map(val, 0, ANALOG_MAX, 0, 5);

    if (val != last_val_[axis]) {
      Control control = trigger_axis(axis, val);
      Serial.println(control);
      last_val_[axis] = val;
    }
  }
};

InputMatrix *input_matrix;
Joystick *range_joystick;

SerialRx serial_rx(IDENTIFIER);

void setup() {
  Serial.begin(9600);
  Serial.println("Booting...");

  input_matrix = new InputMatrix();

  input_matrix->insert(new Button(NAV_ID_TOGGLE, 7, 5));

  input_matrix->insert(new Button(NAV_FREQ_TOGGLE, 7, 4));

  input_matrix->insert(new Encoder(LARGE_NAV_DECR, LARGE_NAV_INCR, 7, 0, 1));
  input_matrix->insert(new Encoder(SMALL_NAV_DECR, SMALL_NAV_INCR, 7, 2, 3));
  input_matrix->insert(new Button(SMALL_NAV_PRESS, 6, 7));

  input_matrix->insert(new Encoder(HDG_DECR, HDG_INCR, 6, 5, 6, true));
  input_matrix->insert(new Button(HDG_PRESS, 6, 4));

#ifdef GFC700
  input_matrix->insert(new Button(AFCS_AP, 0, 8));
  input_matrix->insert(new Button(AFCS_FD, 0, 9));
  input_matrix->insert(new Button(AFCS_HDG, 1, 8));
  input_matrix->insert(new Button(AFCS_ALT, 1, 9));
  input_matrix->insert(new Button(AFCS_NAV, 2, 8));
  input_matrix->insert(new Button(AFCS_VNV, 2, 9));
  input_matrix->insert(new Button(AFCS_APR, 3, 8));
  input_matrix->insert(new Button(AFCS_BC, 3, 9));
  input_matrix->insert(new Button(AFCS_VS, 4, 8));
  input_matrix->insert(new Button(AFCS_UP, 4, 9));
  input_matrix->insert(new Button(AFCS_FLC, 5, 8));
  input_matrix->insert(new Button(AFCS_DN, 5, 9));
#endif  // GFC700

  input_matrix->insert(new Encoder(LARGE_ALT_DECR, LARGE_ALT_INCR, 6, 0, 1));
  input_matrix->insert(new Encoder(SMALL_ALT_DECR, SMALL_ALT_INCR, 6, 2, 3));
  input_matrix->insert(new Button(SMALL_ALT_PRESS, 5, 7));

  input_matrix->insert(new Button(SOFTKEY_1, 5, 6));
  input_matrix->insert(new Button(SOFTKEY_2, 5, 5));
  input_matrix->insert(new Button(SOFTKEY_3, 5, 4));
  input_matrix->insert(new Button(SOFTKEY_4, 5, 3));
  input_matrix->insert(new Button(SOFTKEY_5, 5, 2));
  input_matrix->insert(new Button(SOFTKEY_6, 5, 1));
  input_matrix->insert(new Button(SOFTKEY_7, 5, 0));
  input_matrix->insert(new Button(SOFTKEY_8, 4, 7));
  input_matrix->insert(new Button(SOFTKEY_9, 4, 6));
  input_matrix->insert(new Button(SOFTKEY_10, 4, 5));
  input_matrix->insert(new Button(SOFTKEY_11, 4, 4));
  input_matrix->insert(new Button(SOFTKEY_12, 4, 3));

  input_matrix->insert(new Encoder(LARGE_FMS_DECR, LARGE_FMS_INCR, 0, 0, 1));
  input_matrix->insert(new Encoder(SMALL_FMS_DECR, SMALL_FMS_INCR, 0, 3, 4));
  input_matrix->insert(new Button(SMALL_FMS_PRESS, 0, 2));

  input_matrix->insert(new Button(DIRECT_TO, 1, 6));
  input_matrix->insert(new Button(FPL, 1, 4));
  input_matrix->insert(new Button(CLR, 1, 2));
  input_matrix->insert(new Button(MENU, 1, 5));
  input_matrix->insert(new Button(PROC, 1, 3));
  input_matrix->insert(new Button(ENT, 1, 1));

  input_matrix->insert(new Button(RANGE_PRESS, 1, 7));

  input_matrix->insert(new Encoder(BARO_DECR, BARO_INCR, 2, 3, 4));
  input_matrix->insert(new Encoder(CRS_DECR, CRS_INCR, 2, 5, 6));
  input_matrix->insert(new Button(CRS_PRESS, 2, 2));

  input_matrix->insert(new Encoder(LARGE_COM_DECR, LARGE_COM_INCR, 3, 0, 1));
  input_matrix->insert(new Encoder(SMALL_COM_DECR, SMALL_COM_INCR, 3, 2, 3));
  input_matrix->insert(new Button(SMALL_COM_PRESS, 2, 7));

  input_matrix->insert(new Button(COM_FREQ_TOGGLE, 3, 4));

  input_matrix->insert(new OptoEncoder(RANGE_DECR, RANGE_INCR, 6, 8, 9));
  range_joystick = new Joystick(RANGE_PAN_LEFT, RANGE_PAN_RIGHT, RANGE_PAN_UP,
                                RANGE_PAN_DOWN, 14, 15);
}

void loop() {
  input_matrix->scan_row();
  range_joystick->scan();

  serial_rx.process();
}

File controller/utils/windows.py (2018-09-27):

# Copyright 2018 Flight Lab authors.
#
# Licensed under the Apache License, Version 2.0 (the "License");
# you may not use this file except in compliance with the License.
# You may obtain a copy of the License at
#
#    https://www.apache.org/licenses/LICENSE-2.0
#
# Unless required by applicable law or agreed to in writing, software
# distributed under the License is distributed on an "AS IS" BASIS,
# WITHOUT WARRANTIES OR CONDITIONS OF ANY KIND, either express or implied.
# See the License for the specific language governing permissions and
# limitations under the License.
"""Windows automation library.

This library provides classes to control Windows application and UI.
"""

import os
import psutil
import subprocess
import time
import win32api
import win32con
import win32gui
import win32process

from common import pattern
from utils import app

_SW_SHOW = 5
_SW_MINIMIZE = 6


class WindowNotFoundException(Exception):
  pass


class Window(pattern.EventEmitter, pattern.Worker, pattern.Logger):
  """Class to represent a given window.

  Events:
    "created": when window is found to be created
    "destroyed": when window is found to be destroyed
  """

  def __init__(self,
               name,
               class_name=None,
               window_name=None,
               pid=None,
               *args,
               **kwargs):
    """Creates a Window instance.

    Args:
      name: name of the window.
      class_name: classname attribute of the window on Windows.
      window_name: title of the window.
      pid: id of the process which owns the window.
    """
    super(Window, self).__init__(
        worker_name='Window ({0})'.format(name), *args, **kwargs)
    self._name = name
    self._class_name = class_name
    self._window_name = window_name
    self._pid = pid
    self._found = False

  @property
  def name(self):
    """Gets name of the window."""
    return self._name

  def _get_hwnd_by_pid(self, pid):
    """Gets handle of the window that belongs to a process.

    Args:
      pid: process id.
    Returns:
      Window handle.
    """

    def callback(hwnd, hwnds):
      if win32gui.IsWindowVisible(hwnd) and win32gui.IsWindowEnabled(hwnd):
        _, found_pid = win32process.GetWindowThreadProcessId(hwnd)
        if found_pid == pid:
          hwnds.append(hwnd)
      return True

    hwnds = []
    win32gui.EnumWindows(callback, hwnds)
    return hwnds[0] if hwnds else None

  def exists(self):
    """Checks if the window exists."""
    try:
      self.get_hwnd()
      return True
    except:
      return False

  def get_hwnd(self):
    """Gets handle of the window."""
    if self._class_name or self._window_name:
      hwnd = win32gui.FindWindow(self._class_name, self._window_name)
    elif self._pid:
      hwnd = self._get_hwnd_by_pid(self._pid)
    if not hwnd:
      raise WindowNotFoundException(
          'Window (class name={0}, window name={1}) is not found.'.format(
              self._class_name, self._window_name))
    return hwnd

  def bring_to_foreground(self):
    """Brings the window to foreground."""
    hwnd = self.get_hwnd()
    win32gui.SetForegroundWindow(hwnd)

  def set_style(self, add=None, remove=None):
    """Changes window style.

    Args:
      add: styles to add.
      remove: styles to remove.
    Returns:
      Self.
    """
    hwnd = self.get_hwnd()
    styles = win32gui.GetWindowLong(hwnd, win32con.GWL_STYLE)
    if add:
      styles |= add
    if remove:
      styles &= ~remove
    win32gui.SetWindowLong(hwnd, win32con.GWL_STYLE, styles)
    return self

  def set_position(self, left, top, width, height):
    """Changes window position."""
    hwnd = self.get_hwnd()
    win32gui.SetWindowPos(hwnd, 0, left, top, width, height,
                          win32con.SWP_NOZORDER)
    return self

  def set_size(self, width, height):
    """Changes window size.

    Args:
      width: new width of the window.
      height: new height of the window.
    Returns:
      Self.
    """
    hwnd = self.get_hwnd()
    win32gui.SetWindowPos(hwnd, 0, 0, 0, width, height,
                          win32con.SWP_NOZORDER | win32con.SWP_NOMOVE)
    return self

  def minimize(self):
    """Minimizes the window."""
    hwnd = self.get_hwnd()
    win32gui.ShowWindow(hwnd, win32con.SW_MINIMIZE)
    return self

  def post_message(self, message, wparam, lparam):
    """Posts Windows message to the window.

    Args:
      message: a defined Windows message.
      wparam: parameter of the message.
      lparam: parameter of the message.
    Returns:
      Self.
    """
    hwnd = self.get_hwnd()
    win32api.PostMessage(hwnd, message, wparam, lparam)
    return self

  def _on_start(self):
    self._found = False

  def _on_run(self):
    now_found = self.exists()
    if not self._found and now_found:
      self.logger.debug('[Window - {0}] Created.'.format(self.name))
      self.emit('created', self)
    elif self._found and not now_found:
      self.logger.debug('[Window - {0}] Closed.'.format(self.name))
      self.emit('destroyed', self)
    self._found = now_found

    self._sleep(1)
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

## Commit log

2018-09-17 Fix: update App and WindowsApp status correctly
    [windows.py]
2018-09-21 Fixed app restart issue. Added systemd service setup. Added streaming grpc for component status watching.
    [app.py, windows.py]
2018-09-27 Remove debug print
2018-10-06 update send bug button state.
2018-10-12 Fix indentation of deauth to ensure it always runs
    [badger.py]
2018-12-06 G1000 initial checkin
    [bottom-B.Cu.gbr, bottom-B.Mask.gbr, bottom-B.SilkS.gbr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]
2019-01-12 Use print() function in both Python 2 and Python 3
    Legacy __print__ statements are syntax errors in Python 3 but __print()__ function works as expected in both Python 2 and Python 3.
    [projector_test.py]
2019-01-22 Bug fixes and minor improvement to app component
    [app.py, light.py]
